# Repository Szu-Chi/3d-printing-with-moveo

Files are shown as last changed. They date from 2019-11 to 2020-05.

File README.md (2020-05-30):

# 3D printing with Moveo


### 將BCN3D-Moveo結合ROS、Marlin以及 Ultimaker Cura，產生新型態的3D列印機
我們變更3D列印切片軟體Cura的列印機模型與列印空間，並將Cura與ROS中的逆運動學求解器(IK-Slover)整合，把Cura生成的笛卡爾座標系轉換成更機械軸的轉動角度，最終透過Marlin控制BCN3D-Moveo移動噴嘴進行3D列印
### 系統架構 System Structure
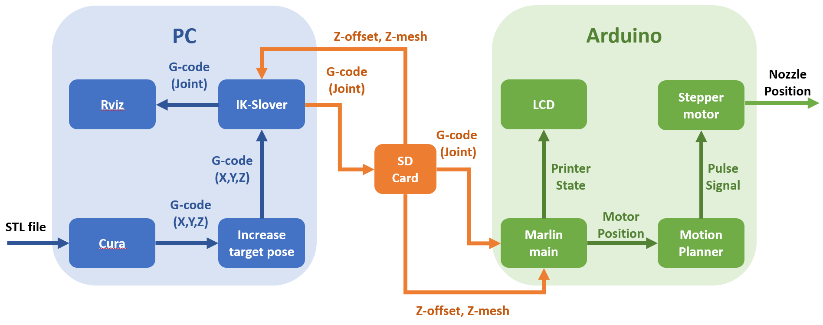
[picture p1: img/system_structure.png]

  
## Demonstration
### 1. 產生g-code與模擬
- 1. [使用Cura(SPIE Lab version)產生g-code](https://www.youtube.com/watch?v=-8nMFFa6ZWg)
- 2. [使用g-code模擬手臂列印](https://www.youtube.com/watch?v=KlCehcnmZSg)
- 3. [使用笛卡兒座標模擬手臂位置](https://www.youtube.com/watch?v=2ucYWZgq9BI)
- 4. [使用各軸轉動角度模擬手臂位置](https://www.youtube.com/watch?v=yYCW1fAp2H8)
### 2. 實際列印
| [寶箱](https://www.youtube.com/watch?v=BejQ-XHtku4) | [摩艾石像](https://www.youtube.com/watch?v=KtgakZhjTZc) | [20X20mm方框(厚度0.6mm)](https://www.youtube.com/watch?v=YZfbAIXzUUw) |
|:---:|:---:|:---:|
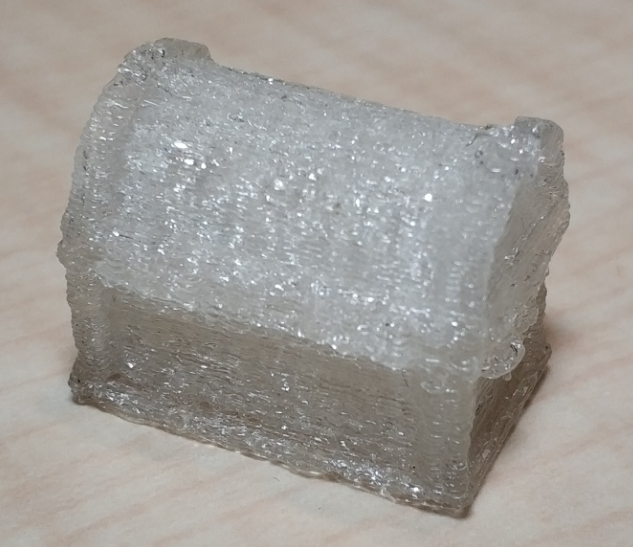
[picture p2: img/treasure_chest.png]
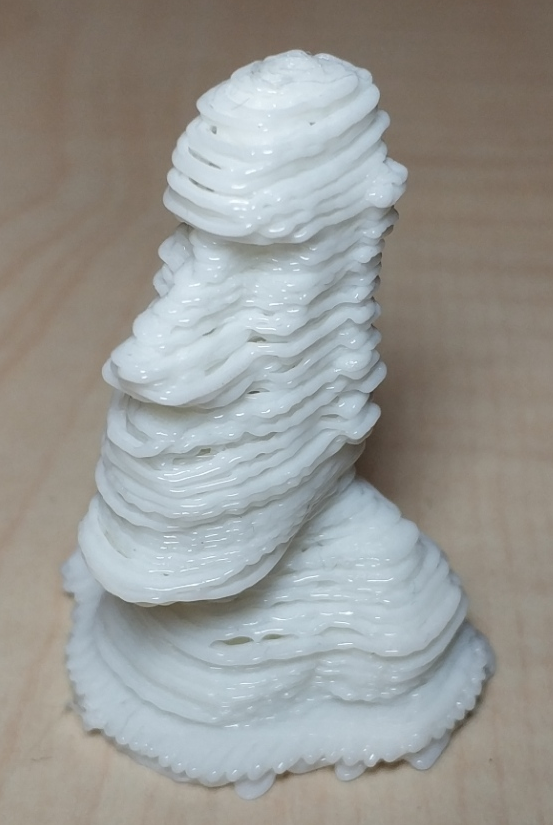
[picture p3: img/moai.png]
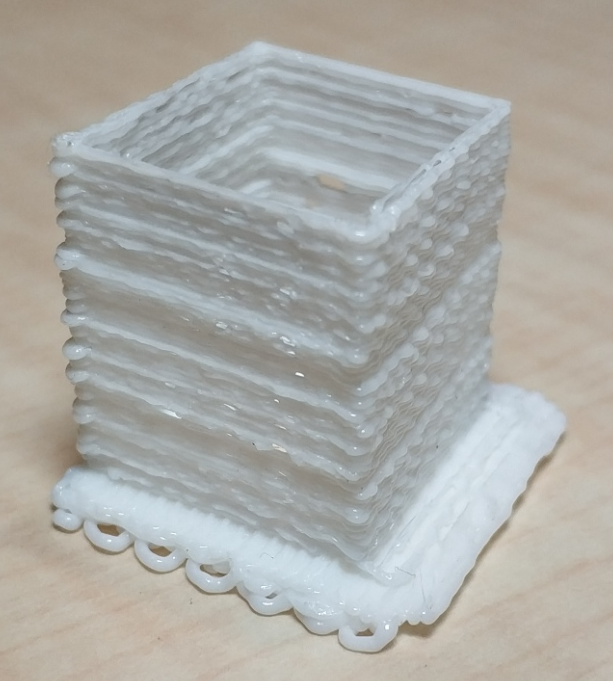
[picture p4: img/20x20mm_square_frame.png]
|  |  |  |
## How to Use
### 1. 環境準備
- 1. 安裝ROS、MoveIt和trac-ik
        1.  安裝ros-melodic-desktop-full\
            參考 [ROS-melodic](http://wiki.ros.org/melodic/Installation/Ubuntu)

        2.  使用原始碼安裝MoveIt\
            參考 [MoveIt](https://moveit.ros.org/install/source/)
        3.  安裝trac-ik
            ```
            sudo apt-get install ros-melodic-trac-ik
            ```
- 2. 建立工作區 moveo_ws
    ```
    cd ~
    mkdir moveo_ws 
    ``` 
- 3. 下載3d-printing-with-movoe資料
    ```
    cd ~/moveo_ws
    git clone https://github.com/Szu-Chi/3d-printing-with-moveo.git
    ``` 
- 4. 變更資料夾名稱為src
    ```
    mv ~/moveo_ws/3d-printing-with-moveo ~/moveo_ws/src
    ``` 
- 5. 建構原始碼build source code
    ```
    catkin_make
    source ~/moveo_ws/devel/setup.bash
    echo "source ~/moveo_ws/devel/setup.bash" >> ~/.bashrc
    ```

### 2. 安裝 Cura SPIE version
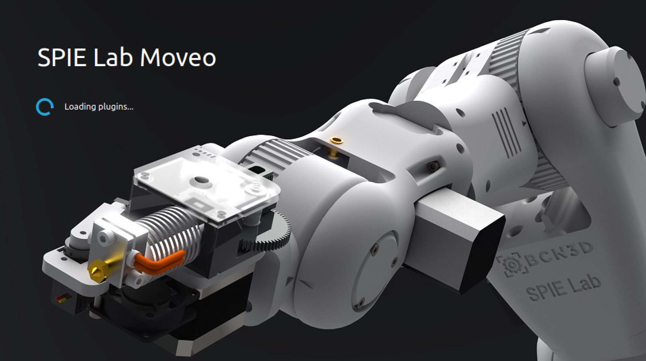
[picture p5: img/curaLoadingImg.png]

- 使用autoInstall.bash
    ```
    cd ~/moveo_ws/src/Cura
    bash autoInstall.bash
    source ~/.bashrc
    ```
or

- 參考 [Running-Cura-from-Source-on-Ubuntu](https://github.com/Ultimaker/Cura/wiki/Running-Cura-from-Source-on-Ubuntu) 手動安裝

### 3. 燒錄Marlin
- 1. 開啟Arduino ~/moveo_ws/src/Marlin/Marlin.ino
- 2. Tool->Board->Arduino Mega or Mega 2560
- 3. 按下上傳按鈕(Ctrl+U) 
### 4. 開始列印
- 1. 開啟Cura
    ```
    cura
    ```
- 2. 放入要列印的STL
- 3. 按下Slice開始切片
- 4. 存檔並等待G-code生成
- 5. 開啟3D列印機
- 6. Prepare->Auto home->Home ALL
- 7. Print from SD
- 8. 開始列印
## About Directories
### CAD
我們更改過後的Moveo，變更內容如下:
- 1. 加上Titan擠出軸以及噴頭組
- 2. 移除木板，新增旋轉台底座
- 3. 變更3M2和4M(加上齒輪組)
- 4. 增進4M1D與3M2之間的穩定度
- 5. 在機構內部新增走線空間

[BCN3D-Moveo 原始版本](https://github.com/BCN3D/BCN3D-Moveo)
### Cura
我們更改過後的Cura，變更內容如下:
- 1. 新增列印機型 SPIE Joint Lab Moveo
- 2. 在機型為Moveo時，改變空間界線判斷方式
- 3. 在機型為Moveo時，連接ROS轉換座標與機械軸位置

[Cura 原始版本](https://github.com/Ultimaker/Cura/wiki/Running-Cura-from-Source-on-Ubuntu) 
### Marlin
我們更改過後的Marlin，變更內容如下:
- 1. 變更Mother Board Arduino腳位
- 2. 馬達歸位方式
- 3. 平面測量方式
- 4. Motion Planner規劃方式

[Marlin 原始版本](https://github.com/MarlinFirmware/Marlin)
### circuit
- 1. Arduino 3D印表機擴充版電路圖及PCB layout\
     [RAMPSv1.6 原始版本](https://github.com/MarlinFirmware/Marlin)

- 2. 馬達閉迴路控制板電路圖及PCB layout\
     [uStepper 原始版本](https://github.com/uStepper/uStepper1)

### gcode_translation
將原始G-code的笛卡爾座標轉換成機械軸

### moveo_moveit_move_group
ROS中用來測試Moveo動作、列印範圍及IK解答效能

### moveo_moveit_config
使用MoveIt Setup Assistant設定Moveo的參數檔(如:各軸活動極限、虛擬機械軸、規劃運動群組...等)，此參數檔用於MoveIt
### moveo_urdf
由SolidWorks外掛模組SW2URDF所生成的Moveo的URDF(Unified Robot Description File)
### progressbar
在Cura切片時產生當前進度條
### simulation
讀取G-code中機械軸的位置，利用Rviz模擬Moveo列印情況
## Troubleshooting
-

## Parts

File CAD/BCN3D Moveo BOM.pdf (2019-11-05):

BCN3D Moveo BOM.xlsx

1

BOM ID | BOM | QUANTITY
1 | Stepper Motor SM42HT47-1684 1,8º step, 1,6 A, 3600 g·cm | 1
2 | ARDUINO MEGA 2560 | 1
3 | Stepper Driver tb6560 | 6
4 | Power Supply 24V 320W | 1
5 | RAMPS V1.4 | 1
6 | Power converter 24V a 12V | 1
7 | Servo Motor 180§ 55G TORQUE=13KG/CM | 1
8 | Gear Ratio 5:1 Planetary Gearbox Nema 17 Stepper 17HS19-1684S-PG5 ( step 0,35º , 2Nm, 1,68A) | 1
9 | Nema 23, 112mm, Ø8mm flat shaft SM57HT112-3004A, step 1,8º, 3A,28Kg·cm | 2
10 | Stepper Motor SM35HT36-1004A, 1,8º step, 1A, 1400g·cm | 1
11 | Stepper Motor nema 17 SM42HT33-1334, 1,8º step, 1,33A, 2200 g·cm | 1
12 | Chrome steel smooth bar-134mm | 1
13 | Chrome steel smooth bar-114mm | 1
14 | Chrome steel smooth bar-80mm | 1
15 | Ball Bearing 608ZZ 8mm x 22mm x 7mm | 10
16 | Ball Bearing 625ZZ 5mm x 16mm x 5mm | 8
17 | Ball Bearing 624ZZ 4mm x 13mm x 5mm | 9
18 | Ball Bearing 623ZZ 3mm x 10mm x 4mm | 3
19 | Brass insert M4 | 3
20 | Brass insert M3 | 20
21 | Pulley T5, Bore 8mm, 14 tooth, 17mm width | 3
22 | Pulley T5, Bore 5mm, 10 tooth, 17 mm width | 2
23 | ROD BAR M8 L 42mm | 1
24 | ZCOUPLING STEEL 5 TO 8 mm rigid | 1
25 | Axial Fan DC 24V 80x80mm | 1
26 | Axial Fan DC 24V 50x50mm | 1
27 | Powwer supply cable IEC 1,8m | 1
28 | Cable USB 2.0 AM/BM 1,8m | 1
29 | Cable Ties | 10
30 | Selfoil bearing 5mm x 8mm x 10mm | 8
31 | Selfoil bearing 8mm x 12mm x 20mm | 2
32 | Wood Base - 550mm x 550mm x 16mm | 1
33 | Breco belt T5, 16mm width, L 180cm | 1,8 m
101 | Dimension A: M-3 Dimension B: 10 mm | 30
102 | Dimension A: M-3 Dimension B: 12 mm | 6
103 | Dimension A: M-3 Dimension B: 16 mm | 13
104 | Dimension A: M-3 Dimension B: 20 mm | 4
105 | Dimension A: M-3 Dimension B: 25 mm | 5
106 | Dimension A: M-3 Dimension B: 30 mm | 2
107 | Dimension A: M-3 Dimension B: 40 mm | 7
108 | Dimension A: M-4 Dimension B: 12 mm | 2
109 | Dimension A: M-4 Dimension B: 10 mm | 2
110 | Dimension A: M-4 Dimension B: 16 mm | 8
111 | Dimension A: M-4 Dimension B: 40 mm | 4
112 | Dimension A: M-4 Dimension B: 45 mm | 6
113 | Dimension A: M-4 Dimension B: 60 mm | 4
114 | Dimension A: M-5 Dimension B: 14 mm | 120
115 | Dimension A: M-5 Dimension B: 20 mm | 8
116 | Dimension A: M-8 Dimension B: 65 mm | 1
117 | Dimension A: M-4 Dimension B: 25 mm | 4
118 | Dimension A: M-3 Nut | 30
119 | Dimension A: M-4 Nut | 4
120 | Dimension A: M-4 Locknut | 18
121 | Dimension A: M-5 Locknut | 16
122 | Dimension A: M-8 Locknut | 2

Components

Fasteners

BCN3D Moveo BOM.xlsx

2

123 | Dimension A: M-4 Dimension B: 20 mm | 3
124 | Dimension A: M-3 Dimension B: 8 mm | 4
125 | Dimension A: M-4 Dimension B: 30 mm | 8
126 | Dimension A: M-3 Dimension B: 35 mm | 4
127 | Washer M-3 | 10
| BOM ID | Parts | Name | Quantity
| 202 | Articulation 1 | 1M1 | 1
| 203 | | 1M2 | 1
| 204 | | 1M3 | 1
| 205 | Articulation 2 | 2M1 | 1
| 206 | | 2M2M | 1
| 207 | | 2M2H | 1
| 208 | | T2M1D | 1
| 209 | | T2M1I | 1
| 210 | Articulation 3 | 3M1 | 1
| 210A | | 3M2C | 1
| 211 | | 3M2 | 1
| 212 | | T3M1 | 1
| 213 | Articulation 4 | 4M1 | 1
| 214 | | 4M2 | 1
| 215 | | 4M2C | 1
| 216 | | T4M1 | 1
| 217 | Machine - tool | Top plate | 1
| 218 | | Bottom plate | 1
| 219 | | Cilinder | 2
| 220 | | Pivot arm | 1
| 221 | | Gripper left | 1
| 222 | | Gripper right | 1
| 223 | | Idol gear | 1
| 224 | | Servo gear | 1
| 225 | Box electronics | Box | 1
| 226 | | Fan module | 1
| 227 | | Suport Drivers | 1
| 228 | Base | Potes | 4
| 229 | Cover | Tapa 2M1 | 2
| 230 | | Tapa 3M1 | 2
| 231 | | Tapa 4M1 | 2
| 232 | | Tapa TBB | 1

Printed Parts

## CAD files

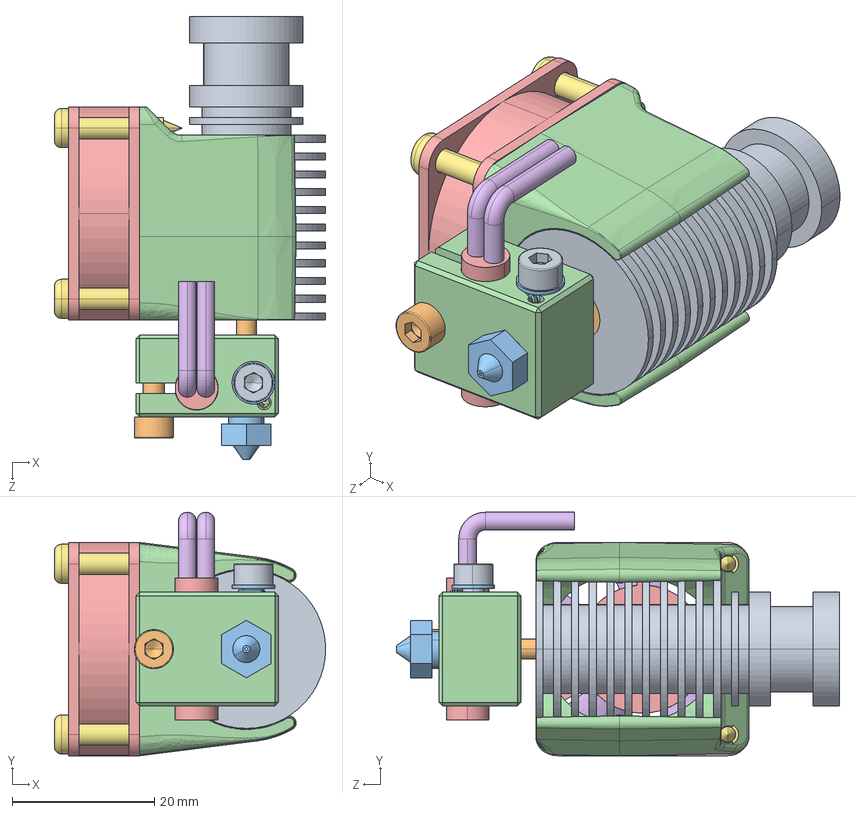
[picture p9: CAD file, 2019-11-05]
CAD/e3d-all-metal-hotend-v6-1.snapshot.2/E3D All Metal Hotend V6 assy.STEP
38.1 x 34.3 x 62.3 mm
E3D v6 HotEnd - Heatsink
E3D v6 HotEnd - Heatbreak
E3D v6 HotEnd - Nozzle
E3D v6 HotEnd - Heat Block
Ceramic Cartridge Heater
Thermistor
HEXAGON SOCKET HEAD CAP SCREWS_SCB3-4
HEXAGON SOCKET HEAD CAP SCREWS_SCB3-10
Flat Washers_PWF3
E3D-v6 Fan Duct
Fan-House-30x30x10-Promoco_Fan-House-KDE0503PFB3-Promoco
Fan-30x30x10-Promoco_Fan-KDE0503PFB3-Promoco
Self Tapping Screws - Pan Head_CSPTRSA-SUS-TP3-16 x 4

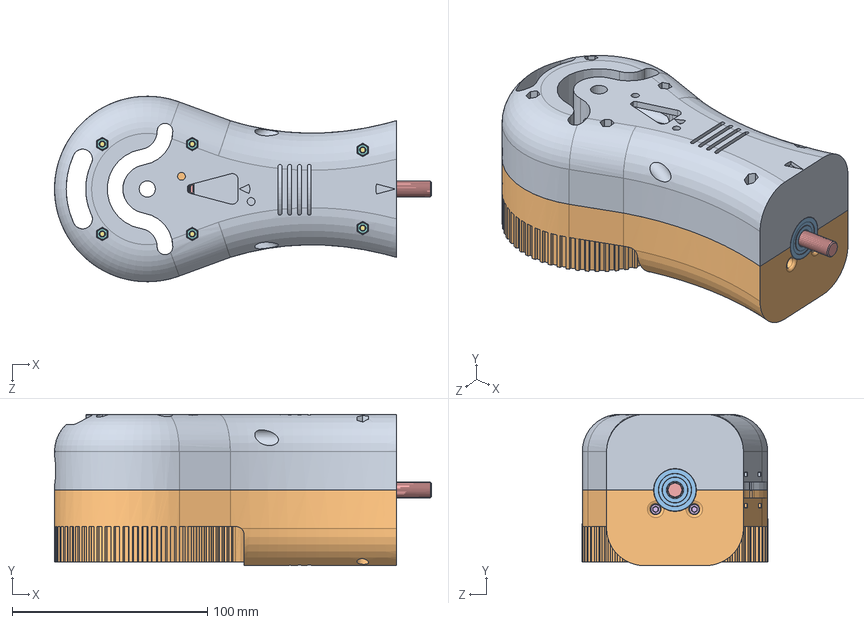
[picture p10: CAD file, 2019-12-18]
CAD/BCN3D-Moveo-master(1)/CAD files/3M2.SLDASM
193.0 x 77.5 x 95.0 mm
3M2C
3M2CC
8mm Bearing
Coupling 5 to 8 mm
Smooth bar 8mm x 50mm
M3x10 x 2
M3x40 x 6
M3 Nut x 6
35stepper with gearbox
limit button
Via Hole-Part-1 x 4
Pad U1-3(781.496mil,670.748mil) on Bottom Layer-Part-1
Track (945mil,777.5mil)(945mil,787.5mil) on Bottom Layer-Part-1
Track (932.5mil,765mil)(945mil,777.5mil) on Bottom Layer-Part-1
Track (922.5mil,765mil)(932.5mil,765mil) on Bottom Layer-Part-1
Track (878.248mil,720.748mil)(922.5mil,765mil) on Bottom Layer-Part-1
Track (781.496mil,720.748mil)(878.248mil,720.748mil) on Bottom Layer-Part-1
Pad U1-2(781.496mil,720.748mil) on Bottom Layer-Part-1
Pad C4-1(945mil,787.5mil) on Bottom Layer-Part-1
Track (470mil,610mil)(480.748mil,620.748mil) on Bottom Layer-Part-1
Track (480.748mil,620.748mil)(596.456mil,620.748mil) on Bottom Layer-Part-1
Pad U1-5(596.456mil,620.748mil) on Bottom Layer-Part-1
Pad R5-2(470mil,610mil) on Bottom Layer-Part-1
Track (910mil,955mil)(1010mil,955mil) on Bottom Layer-Part-1
Pad Hole-Part-1 x 36
Bottom Layer-Part-1 x 29
Top Layer-Part-1 x 29
Track (1010mil,260mil)(1010mil,455mil) on Bottom Layer-Part-1
Track (910mil,260mil)(910mil,455mil) on Bottom Layer-Part-1
Track (810mil,260mil)(810mil,455mil) on Bottom Layer-Part-1
Track (710mil,260mil)(710mil,455mil) on Bottom Layer-Part-1
Pad Copper-Part-1
Pad Copper-Part-1-1
Track (610mil,955mil)(652.5mil,912.5mil) on Bottom Layer-Part-1
Track (610mil,955mil)(610mil,1060mil) on Bottom Layer-Part-1
Track (652.5mil,912.5mil)(1057.5mil,912.5mil) on Bottom Layer-Part-1
Track (1057.5mil,912.5mil)(1079.472mil,890.528mil) on Bottom Layer-Part-1
Track (1118.158mil,606.842mil)(1118.158mil,649.528mil) on Bottom Layer-Part-1
Track (1079.472mil,688.213mil)(1118.158mil,649.528mil) on Bottom Layer-Part-1
Track (1079.472mil,688.213mil)(1079.472mil,890.528mil) on Bottom Layer-Part-1
Pad R2-1(610mil,1060mil) on Bottom Layer-Part-1
Track (1032.9mil,914.472mil)(1079.472mil,867.9mil) on Top Layer-Part-1
Track (710mil,955mil)(750.528mil,914.472mil) on Top Layer-Part-1
Track (750.528mil,914.472mil)(1032.9mil,914.472mil) on Top Layer-Part-1
Track (1079.472mil,745.528mil)(1120mil,705mil) on Top Layer-Part-1
Track (1079.472mil,745.528mil)(1079.472mil,867.9mil) on Top Layer-Part-1
Track (810mil,955mil)(854mil,999mil) on Top Layer-Part-1
Track (854mil,999mil)(1040mil,999mil) on Top Layer-Part-1
Track (1040mil,999mil)(1053.472mil,985.528mil) on Top Layer-Part-1
Track (1053.472mil,918.9mil)(1053.472mil,985.528mil) on Top Layer-Part-1
Track (1120mil,805mil)(1120mil,852.373mil) on Top Layer-Part-1
Track (1053.472mil,918.9mil)(1120mil,852.373mil) on Top Layer-Part-1
Track (510mil,955mil)(510mil,1055mil) on Bottom Layer-Part-1
Track (510mil,1055mil)(515mil,1060mil) on Bottom Layer-Part-1
Track (295mil,955mil)(510mil,955mil) on Bottom Layer-Part-1
Track (170mil,830mil)(295mil,955mil) on Bottom Layer-Part-1
Pad R1-1(515mil,1060mil) on Bottom Layer-Part-1
Pad Copper-Part-1-2
Pad Copper-Part-1-3
Track (572.905mil,872.725mil)(576.535mil,869.095mil) on Top Layer-Part-1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

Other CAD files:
CAD/BCN3D-Moveo-master(1)/CAD files/1M1A.SLDPRT
CAD/BCN3D-Moveo-master(1)/CAD files/1M1B.SLDPRT
CAD/BCN3D-Moveo-master(1)/CAD files/1M2A-1.SLDPRT
CAD/BCN3D-Moveo-master(1)/CAD files/1M2A-2.SLDPRT
CAD/BCN3D-Moveo-master(1)/CAD files/1M2A.SLDPRT
CAD/BCN3D-Moveo-master(1)/CAD files/1M3.SLDASM
CAD/BCN3D-Moveo-master(1)/CAD files/1M3A.SLDPRT
CAD/BCN3D-Moveo-master(1)/CAD files/2.SLDASM
CAD/BCN3D-Moveo-master(1)/CAD files/2M1D.SLDPRT
CAD/BCN3D-Moveo-master(1)/CAD files/2M2 assembly.SLDASM
CAD/BCN3D-Moveo-master(1)/CAD files/2M2HA.SLDPRT
CAD/BCN3D-Moveo-master(1)/CAD files/2M2M assembly.SLDASM
CAD/BCN3D-Moveo-master(1)/CAD files/2M2MA.SLDPRT
CAD/BCN3D-Moveo-master(1)/CAD files/2M_installHelper.SLDPRT
CAD/BCN3D-Moveo-master(1)/CAD files/35stepper with gearbox.SLDPRT
CAD/BCN3D-Moveo-master(1)/CAD files/3M1D.SLDPRT
CAD/BCN3D-Moveo-master(1)/CAD files/3M2C.SLDPRT
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

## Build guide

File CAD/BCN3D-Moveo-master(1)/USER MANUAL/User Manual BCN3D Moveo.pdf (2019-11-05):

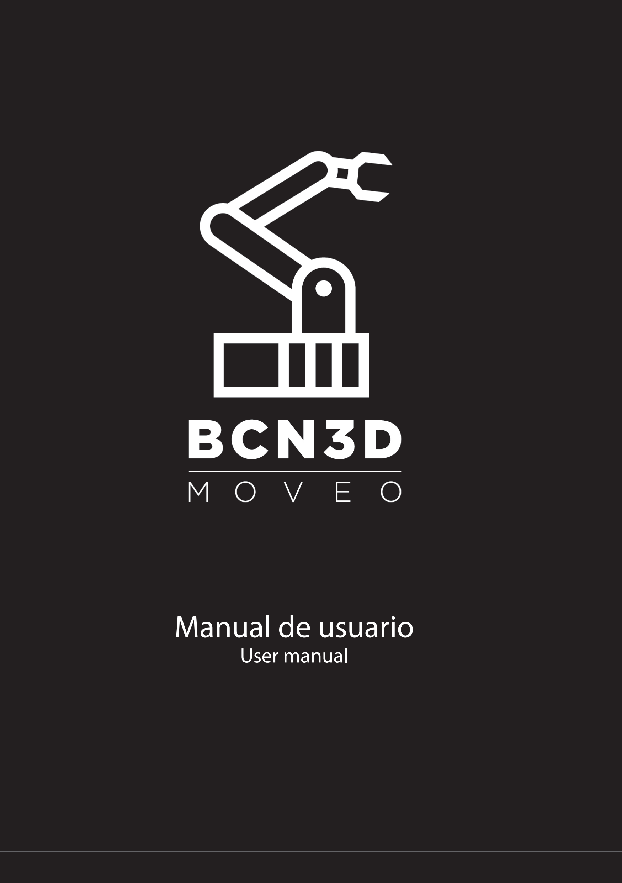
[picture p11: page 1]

# Manual de usuario

# User manual

2 - Manual de usuario User manual

Manual de montaje
Assembly manual

Manual de usuario User manual

¿Cómo usar el BCN3D Moveo? How to use the BCN3D Moveo?

Instalación del firmware
Firmware installation

Sobre el BCN3D Moveo
About de BCN3D Moveo

## ÍNDICE INDEX

3 - 4

6 - 39

40 - 42

43 - 45

Manual de usuario User manual - 3

## Sobre el BCN3D Moveo About the BCN3D Moveo

BCN3D Technologies sigue dando pasos importantes para cumplir con su objetivo de acercar las tecnologías de fabricación digital y aditiva al público general. En esta ocasión queremos presentar el BCN3D Moveo, un brazo robótico diseñado desde cero y desarrollado por nuestros ingenieros en colaboración con el Departament d’Ensenyament de la Generalitat de Catalunya, cuya estructura está impresa en 3D y su tecnología controlada por el software Arduino.
Moveo, totalmente funcional a día de hoy, ha nacido, como todos los demás productos salidos de BCN3D Technologies, con voluntad formativa y abierta.

EL PORQUÉ DE BCN 3D MOVEO

Una de las preocupaciones del Departament d’Ensenyament es el elevado coste de los materiales que deben usar los alumnos de formación de grado para realizar sus prácticas. En este sentido, un brazo robótico Open Source, modificable por los alumnos y reproducible a bajo coste podía copar varios de los itinerarios formativos existentes: Diseño mecánico, automatismos, programación industrial, etc.
Así pues, el BCN3D Moveo debería permitir a los institutos disfrutar de un equipamiento personalizable, modificable y de fácil acceso para el alumno a un precio lejos de los equipamientos industriales que normalmente habían tenido que adquirir, pero con unas prestaciones suficientes para los fines formativos.
Como área de la Fundació CIM, BCN3D Technologies comparte la vocación formativa de su alma máter. Es por dicho motivo que cuando el Departament d’Ensenyament se puso en contacto con nosotros para proponernos el proyecto un año atrás, no dudamos en aceptar la propuesta.
Una vez tuvimos el brazo diseñado y fabricado, se inició la última parte del proyecto que consistía en un workshop de montaje y puesta en marcha para 15 institutos de Cataluña, realizado en las instalaciones de BCN3D Technologies.
Estos institutos ya cuentan con el BCN3D Moveo en sus aulas y talleres, y deberán presentar prácticas que acrediten su conocimiento del equipo durante el mes de setiembre.

BCN3D Technologies keeps taking important steps in order to achieve his goal of bringing the digital manufacturing technology to everyone. In this occasion we are presenting the BCN3D Moveo, a robotic arm design from scratch and developed by our engineers in collaboration with the Departament d’Ensenyament from the Generalitat de Catalunya. Its structure is fully printed using additive manufacturing technologies and its electronics are controlled by the software Arduino.
Moveo, fully functional nowadays, has been born, as all the BCN3D Technologies products, with an open and educational wish.

WHY BCN 3D MOVEO

One of the Departament d’Ensenyament worries is the high price of the materials the grade students must use on their internships. Holding that in mind, an Open Source robotic arm, adaptable by the students and low cost reproducible could take several educational itineraries: mechanical design, automatism, industrial programing, etc.
Thus, the BCN3D Moveo should allow the educational centers to enjoy a modifiable and easily accessible for the students, at a price far lower than the usual industrial equipment they used to have to acquire, with enough output for training purposes. As a Fundació CIM area, BCN3D Technologies shares its educational vocation. That is the reason why when the Departament d’Ensenyament contacted us in order to suggest and offer this project a year ago we didn’t hesitate on taking that opportunity. Once we had the robotic arm designed and manufactured we started the last phase of the project, which consisted on an assembling and fine tuning workshop for 15 institutes around Catalonia, which took place in the BCN3D Technologies.
These institutes already have the BCN3D Moveo in their classrooms and workshops, and will have to present an internship program that proves their knowledge about the arm during September.

## Sobre el BCN3D Moveo About the BCN3D Moveo

TECNOLOGÍA OPEN SOURCE: LA PLATAFORMA
GITHUB

Como hiciéramos con todos nuestros productos, los archivos del BCN3D Moveo estarán a la disposición de todo aquel que quiera acceder a ellos. Gracias a la plataforma Github, un espacio en el que los usuarios comparten sus diseños de forma libre, cualquier persona podrá obtener toda la información necesaria para montarse su propio BCN3D Moveo en casa.
A diferencia de los otros productos de BCN3D Technologies, el BCN3D Moveo no será comercializado. El proyecto se ha realizado con el ánimo de dar una aportación más a la comunidad a partir de la idea del Departament d’Ensenyament.
BCN3D liberará el conocimiento del Moveo en sus repositorios en Github como se ha venido haciendo con los productos oficiales de BCN3D Techologies. De esta manera, se espera que la comunidad y los centros formativos que estén interesados puedan fabricar sus propios robots.
Así, entre los archivos que subiremos a dicha plataforma incluimos el “bill of materials” (BOM), en el que se detallan todos los componentes necesarios para montar el brazo, así como los diseños CAD, para que todo el mundo pueda modificar el diseño del BCN3D Moveo a su gusto. De la misma forma, los usuarios de Github podrán encontrar los archivos STL para la impresión de la estructura del brazo, y el manual de montaje del mismo que estará en español e inglés.
Gracias a este proyecto impulsado por el Departament d’Ensenyament y desarrollado por BCN3D Technologies, todo el mundo podrá fabricarse un brazo robótico en casa, sin necesidad de tener un amplio conocimiento técnico. Así, os animamos a todos a fabricaros el BCN3D Moveo y compartir los resultados en las redes con el hashtag #BCN3DMoveo.

OPEN SOURCE TECHNOLOGY: GITHUB

As we have done with all our developed pordutcs, the BCN3D Moveo files will be available for everyone. Thanks to the platform Github, a website where users around the world share their designs, anyone will be able to obtain all the necessary information in order to assemble his own BCN3D Moveo at home.
Unlike the other BCN3D products, the Moveo won’t be commercialized. The project has been born and developed in order to make a move for the community progress starting from the Departament d’Ensenyament idea.
Nevertheless, BCN3D will fee all the Moveo know how on our Github account, as we have been doing with all the BCN3D Technologies products. Thus, the users will be able to find the bill of material (BOM), where all the needed components for the assembling of the arm come detailed, as the CAD designs, so anyone will be able to modify the BCN3D Moveo design as they wish.
Furthermore, the Github users will find the STL files for the structure printing and the assembling, fine tuning and firmware upload manuals, which will be available both in English and Spanish.
Thanks to this project motivated by the Departament d’Ensenyament and developed by BCN3D Technologies everyone will be able to fabricate their own robotic arm at home, no highly technical knowledge needed. Therefore, we encourage you to fabricate the BCN3D Moveo and share the results on the social networks using the hashtag #BCN3DMoveo.

# Manual de montaje

# Assembly manual

## Montaje del módulo 1 Module 1

x8

BOM | Descripción Description | Cant Qty
115 | Tornillo M5 x 20mm Screw M5 x 20mm | 8
16 | Rodamiento 5mm x 16mm x 5mm Bearing 5mm x 16mm x 5mm | 8
30 | Espaciador 5mm x 10mm Spacer 5mm x 10mm | 8

121 | Tuerca autoblocante M5 M5 locknut | 8
15 | Rodamiento 8mm x 22mm x 7mm Bearing 8mm x 22mm x 7mm | 2
- | 1M2A Base rotatoria 1M2A Rotary plate | 1

## Montaje del módulo 1 Module 1 assembly

x1

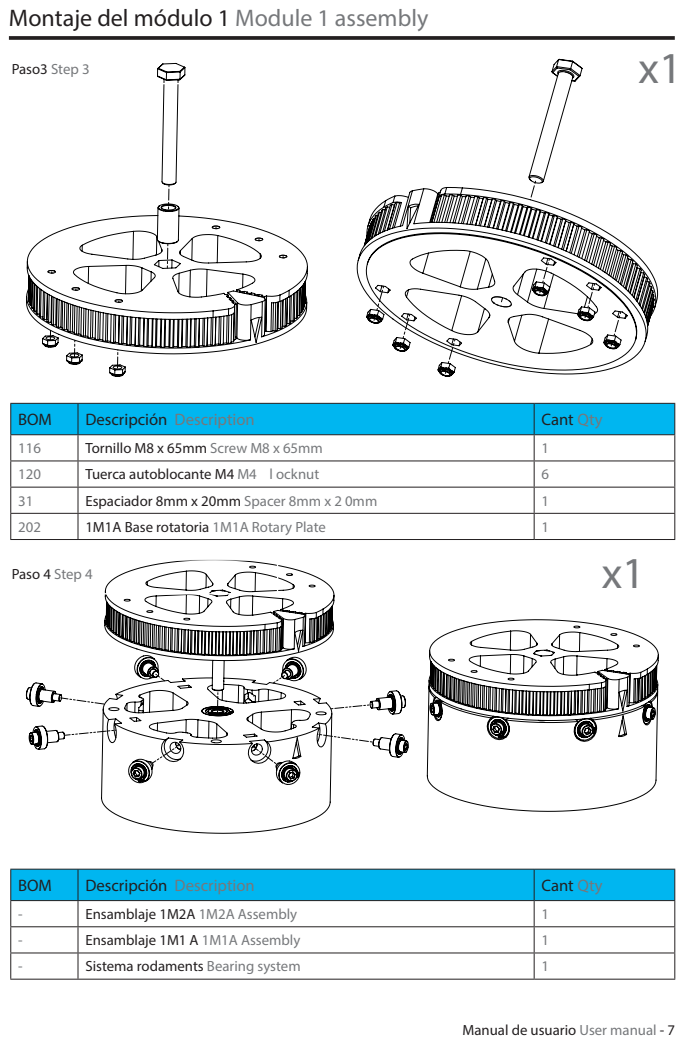
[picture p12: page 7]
Paso3 Step 3; Paso 4 Step 4

BOM | Descripción Description | Cant Qty
116 | Tornillo M8 x 65mm Screw M8 x 65mm | 1
120 | Tuerca autoblocante M4 M4 l ocknut | 6
31 | Espaciador 8mm x 20mm Spacer 8mm x 2 0mm | 1
202 | 1M1A Base rotatoria 1M1A Rotary Plate | 1

- | Ensamblaje 1M2A 1M2A Assembly | 1
- | Ensamblaje 1M1 A 1M1A Assembly | 1
- | Sistema rodaments Bearing system | 1

## Montaje del módulo 1 Module 1 assembly

BOM ID | Descripción Description | Cant Qty
204 | Pieza impresa 1M3 Printed part 1M3 | 1
1 | Motor nema 17 largo Large nema 17 motor | 1
101 | Tornillo M3 x 10mm M3 x 8mm screw | 4
22 | Polea 5mm 5mm pulley | 1

## Montaje del módulo 2 Module 2 assembly

x1

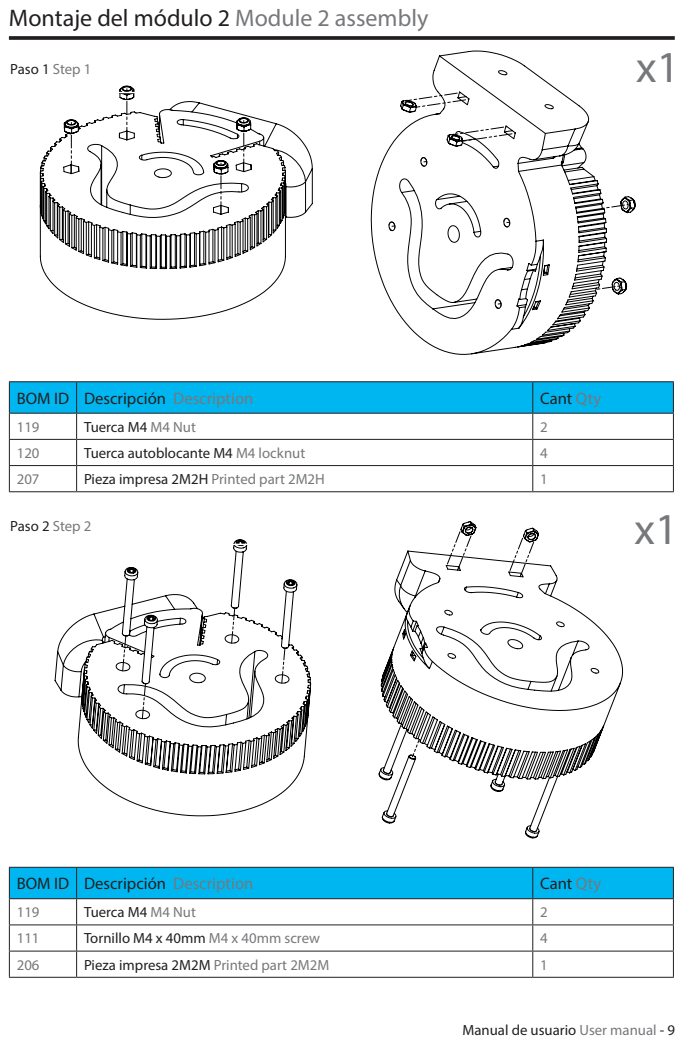
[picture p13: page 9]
Paso 1 Step 1; Paso 2 Step 2

BOM ID | Descripción Description | Cant Qty
119 | Tuerca M4 M4 Nut | 2
120 | Tuerca autoblocante M4 M4 locknut | 4
207 | Pieza impresa 2M2H Printed part 2M2H | 1

111 | Tornillo M4 x 40mm M4 x 40mm screw | 4
206 | Pieza impresa 2M2M Printed part 2M2M | 1

## Montaje del módulo 2 Module 2 assembly

BOM ID | Descripción Description | Cant Qty
- | Ensamblaje 2M2H 2M2H assembly | 2
- | Ensamblaje 2M2M 2M2M assembly | 2

## Montaje del módulo 2 Module 2 assembly

x1

BOM ID | Descripción Description | Cant Qty
208 | Pieza impresa T2M1D Printed part T2M1D | 1
117 | Tornillo M4 x 20mm M4 x 20mm screw | 1
119 | Tuerca M4 M4 nut | 1
118 | Tuerca M3 M3 nut | 1
17 | Rodamiento 4mm x 13mm x 5mm Bearing 4mm x 13mm x 5mm | 3

209 | Pieza impresa T2M1I Printed part T2M 1I | 1

## Montaje del módulo 2 Module 2 assembly

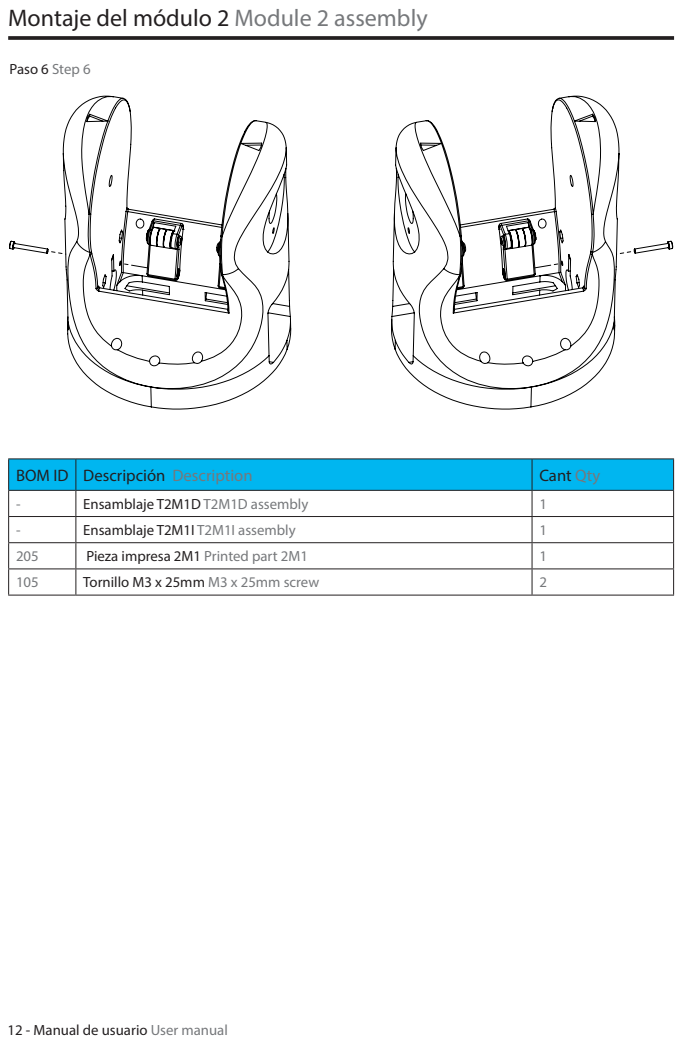
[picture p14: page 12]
Paso 6 Step 6

BOM ID | Descripción Description | Cant Qty
- | Ensamblaje T2M1D T2M1D assembly | 1
- | Ensamblaje T2M1I T2M1I assembly | 1
205 | Pieza impresa 2M1 Printed part 2M1 | 1
105 | Tornillo M3 x 25mm M3 x 25mm screw | 2

## Montaje del módulo 2 Module 2 assembly

BOM ID | Descripción Description | Cant Qty
9 | Motor Nema 23 Nema 23 motor | 2
114 | Tornillo M5 x 14mm M5 x 14mm screw | 8
121 | Tuerca autoblocante M5 M5 locknut | 8

## Montaje del módulo 2 Module 2 assembly

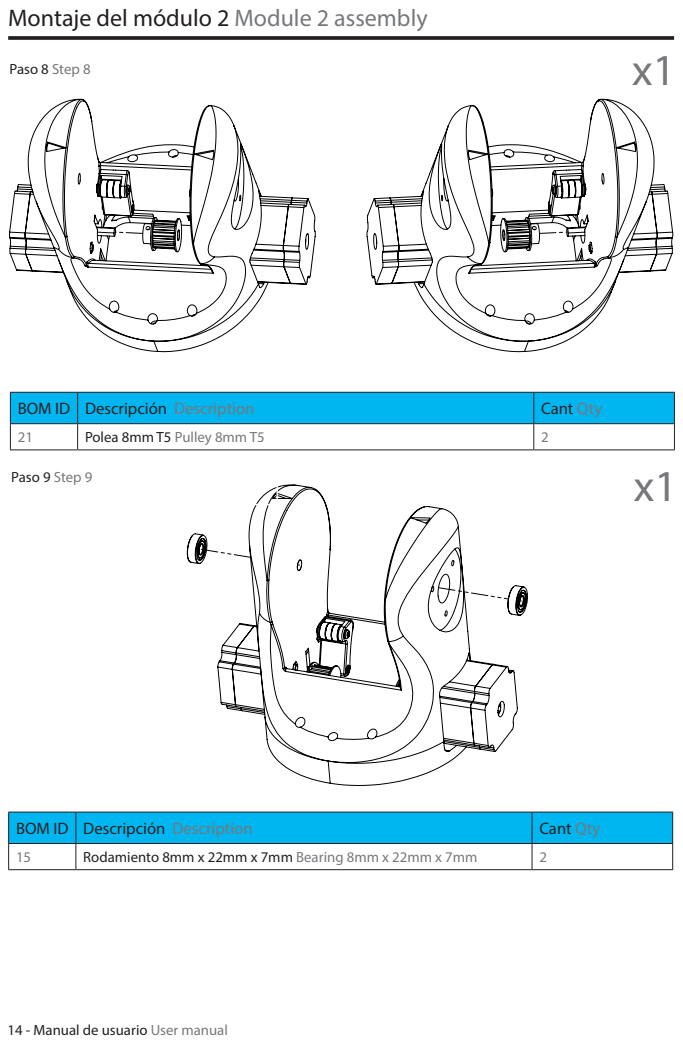
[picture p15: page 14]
Paso 8 Step 8; Paso 9 Step 9

BOM ID | Descripción Description | Cant Qty
21 | Polea 8mm T5 Pulley 8mm T5 | 2

15 | Rodamiento 8mm x 22mm x 7mm Bearing 8mm x 22mm x 7mm | 2

## Montaje del módulo 2 Module 2 assembly

BOM ID | Descripción Description | Cant Qty
- | Ensamblaje 2M2 2M2 assembly | 1

12 | Barra lisa 134mm Smooth bar 134mm | 1

## Montaje del módulo 2 Module 2 assembly

BOM ID | Descripción Description | Cant Qty
19 | Inserto M4 M4 insert | 2

20 | Inserto M3 M3 insert | 2
101 | Tornillo M3 x 10mm M3 x 10mm screw | 6
229 | Pieza impresa Tapa 2M1 Printed part Tapa 2M1 | 1

## Montaje de la herramienta Tool assembly

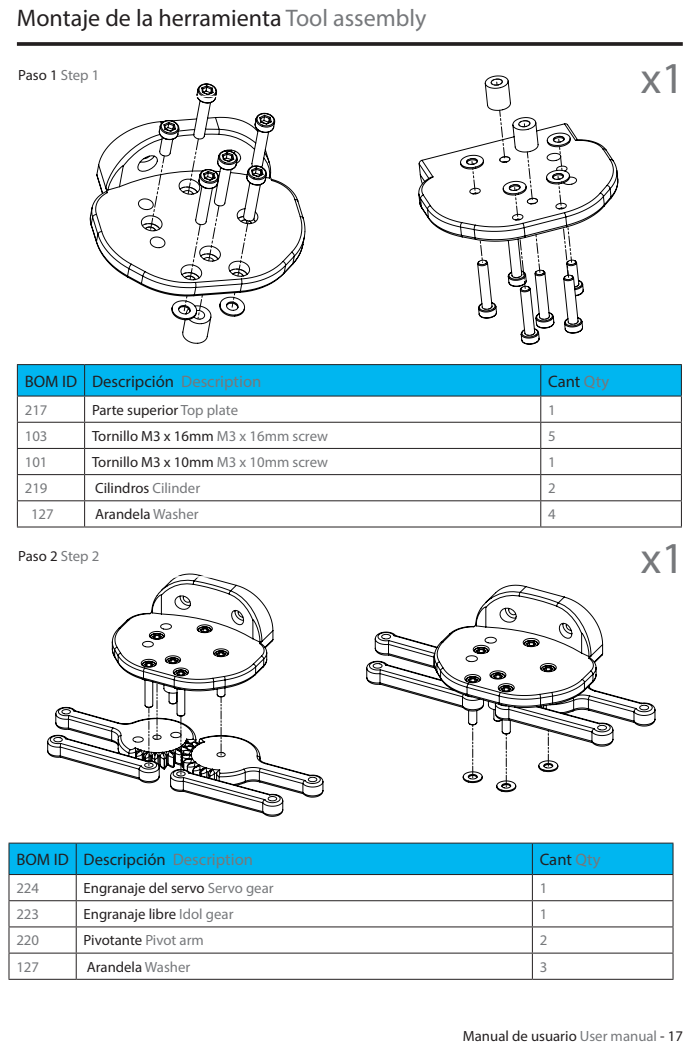
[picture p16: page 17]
Paso 1 Step 1; Paso 2 Step 2

BOM ID | Descripción Description | Cant Qty
217 | Parte superior Top plate | 1
103 | Tornillo M3 x 16mm M3 x 16mm screw | 5
101 | Tornillo M3 x 10mm M3 x 10mm screw | 1
219 | Cilindros Cilinder | 2
127 | Arandela Washer | 4

224 | Engranaje del servo Servo gear | 1
223 | Engranaje libre Idol gear | 1
220 | Pivotante Pivot arm | 2
127 | Arandela Washer | 3

## Montaje de la herramienta Tool assembly

BOM ID | Descripción Description | Cant Qty
218 | Parte inferior Bottom plate | 1
118 | Tuerca M3 M3 nut | 4

221 | Pinza izquiera Left gripper | 1
222 | Pinza derecha Right gripper | 1
103 | Tornillo M3 x 16mm M3 x 16mm screw | 8

## Montaje del módulo 3 Module 3 assembly

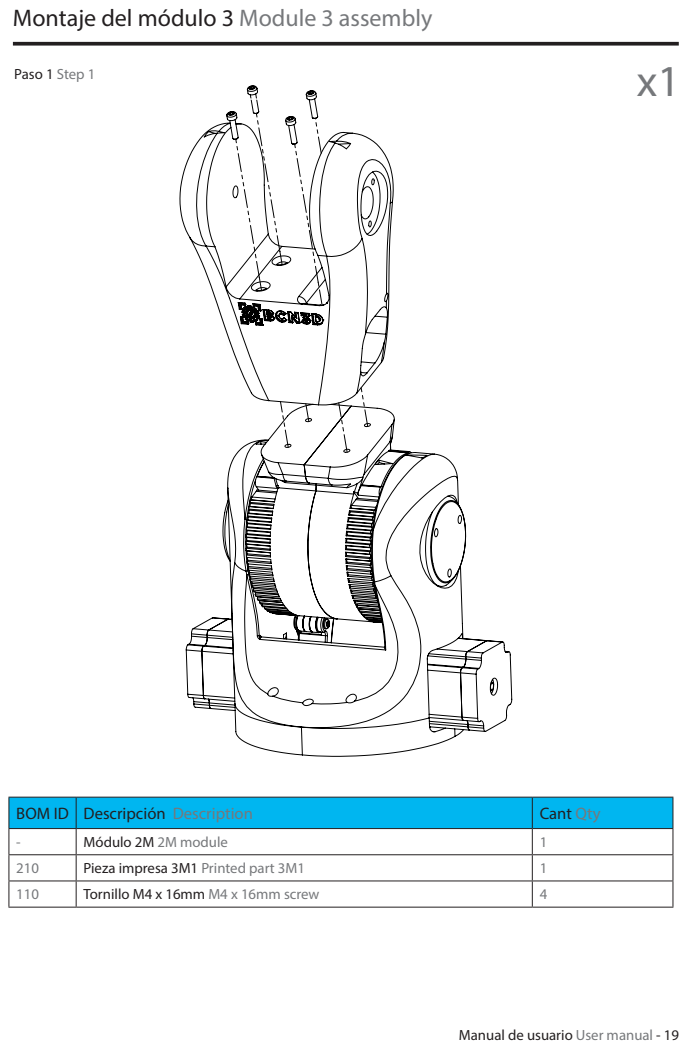
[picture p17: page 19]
Paso 1 Step 1

BOM ID | Descripción Description | Cant Qty
- | Módulo 2M 2M module | 1
210 | Pieza impresa 3M1 Printed part 3M1 | 1
110 | Tornillo M4 x 16mm M4 x 16mm screw | 4

## Montaje del módulo 3 Module 3 assembly

BOM ID | Descripción Description | Cant Qty
212 | Pieza impresa T3M1 Printed part T3M1 | 1
17 | Rodamiento 4mm x 13mm x 5mm Bearing 4mm x 13mm x 5mm | 3
123 | Tornillo M4 x 20mm M4 x 20mm screw | 1
119 | Tuerca M4 M4 nut | 1

- | Módulo T3M1 T3M1 module | 1
107 | Tornillo M3 x 40mm M3 x 40mm screw | 1
118 | Tuerca M3 M3 nut | 1

## Montaje del módulo 3 Module 3 assembly

BOM ID | Descripción Description | Cant Qty
210A | Pieza impresa 3M2C Printed part 3M2C | 1
11 | Motor Nema-17 34mm Nema-17 motor 34mm | 1
101 | Tornillo M3 x 10mm M3 x 10mm screw | 2

24 | Acoplador 8mm - 5mm Coupling 8mm- 5mm | 1
23 | Barra roscada 42mm Rod bar 42mm | 1
15 | Rodamiento 8mm x 22mm x 7mm Bearing 8mm x 22mm x 7mm | 1

## Montaje del módulo 4 Module 4 assembly

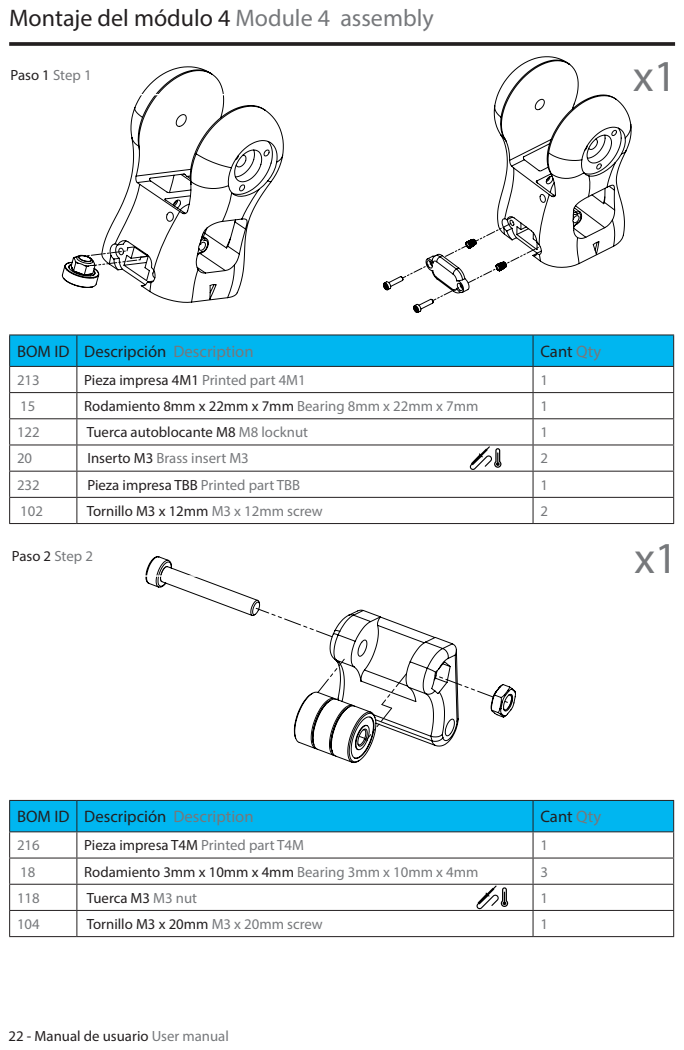
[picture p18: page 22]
Paso 1 Step 1; Paso 2 Step 2

BOM ID | Descripción Description | Cant Qty
213 | Pieza impresa 4M1 Printed part 4M1 | 1
15 | Rodamiento 8mm x 22mm x 7mm Bearing 8mm x 22mm x 7mm | 1
122 | Tuerca autoblocante M8 M8 locknut | 1
20 | Inserto M3 Brass insert M3 | 2
232 | Pieza impresa TBB Printed part TBB | 1
102 | Tornillo M3 x 12mm M3 x 12mm screw | 2

216 | Pieza impresa T4M Printed part T4M | 1
18 | Rodamiento 3mm x 10mm x 4mm Bearing 3mm x 10mm x 4mm | 3
118 | Tuerca M3 M3 nut | 1
104 | Tornillo M3 x 20mm M3 x 20mm screw | 1

## Montaje del módulo 4 Module 4 assembly

BOM ID | Descripción Description | Cant Qty
214 | Pieza impresa 4M2 Printed part 4M2 | 1
215 | Pieza impresa 4M2C Printed part 4M2C | 1
118 | Tuerca M3 M3 nut | 3
117 | Tornillo M4 x 25mm M4 x 25mm screw | 2
120 | Tuerca autoblocante M4 M4 Locknut | 4

## Montaje del módulo 4 Module 4 assembly

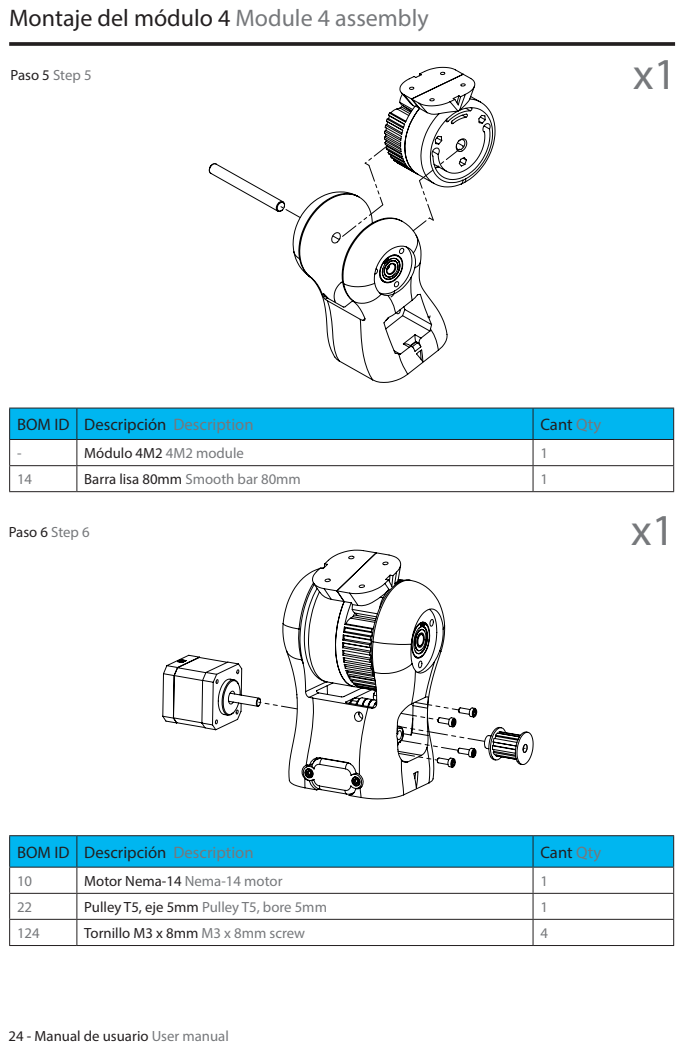
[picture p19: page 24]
Paso 5 Step 5; Paso 6 Step 6

BOM ID | Descripción Description | Cant Qty
- | Módulo 4M2 4M2 module | 1
14 | Barra lisa 80mm Smooth bar 80mm | 1

10 | Motor Nema-14 Nema-14 motor | 1
22 | Pulley T5, eje 5mm Pulley T5, bore 5mm | 1
124 | Tornillo M3 x 8mm M3 x 8mm screw | 4

## Montaje del módulo 4 Module 4 assembly

BOM ID | Descripción Description | Cant Qty
20 | Inserto M3 M3 insert | 6
231 | Pieza impresa Tapa 4M1 Printed part tapa 4M1 | 6
102 | Tornillo M3 x 12mm M3 x 12mm screw | 2

- | Módulo herramienta Tool module | 1
103 | Tornillo M3 x 16mm M3 x 16mm screw | 4

## Montaje del módulo 4 Module 4 assembly

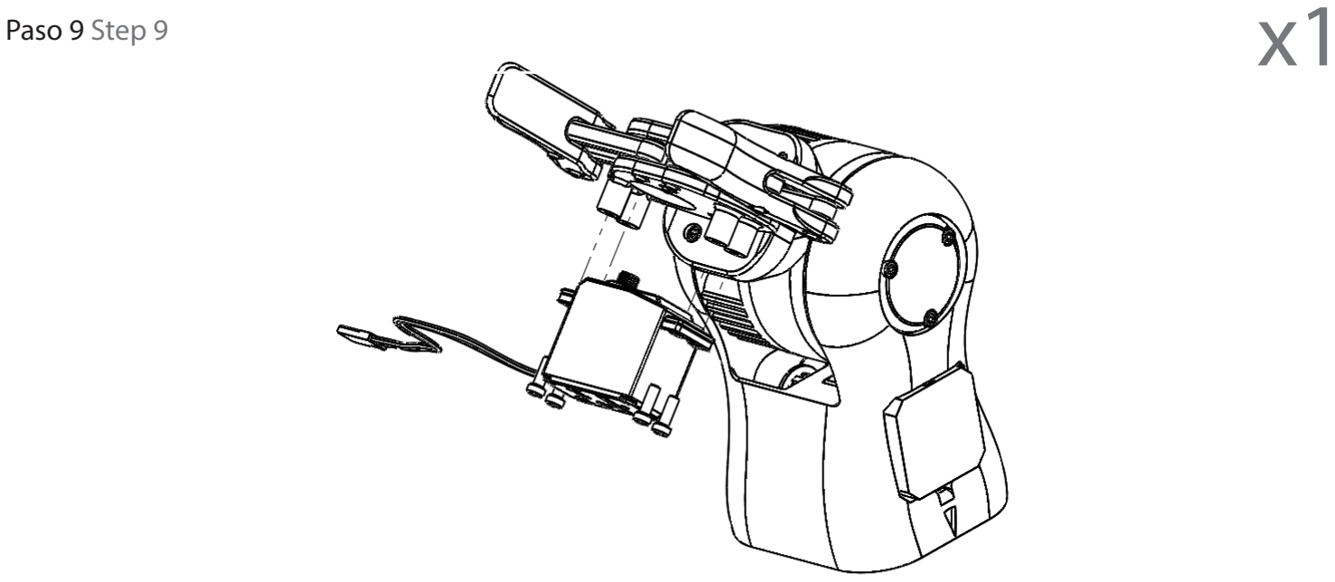
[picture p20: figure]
Paso 9 Step 9

BOM ID | Descripción Description | Cant Qty
7 | Servo motor Servo motor | 1
101 | Tornillo M3 x 10mm M3 x 10mm screw | 4

## Montaje del módulo 3 Module 3 assembly

BOM ID | Descripción Description | Cant Qty
- | Ensamblaje módulo 4 Tool module | 1
103 | Tornillo M3 x 16mm M3 x 16mm screw | 4

## Montaje del módulo 3 Module 3 assembly

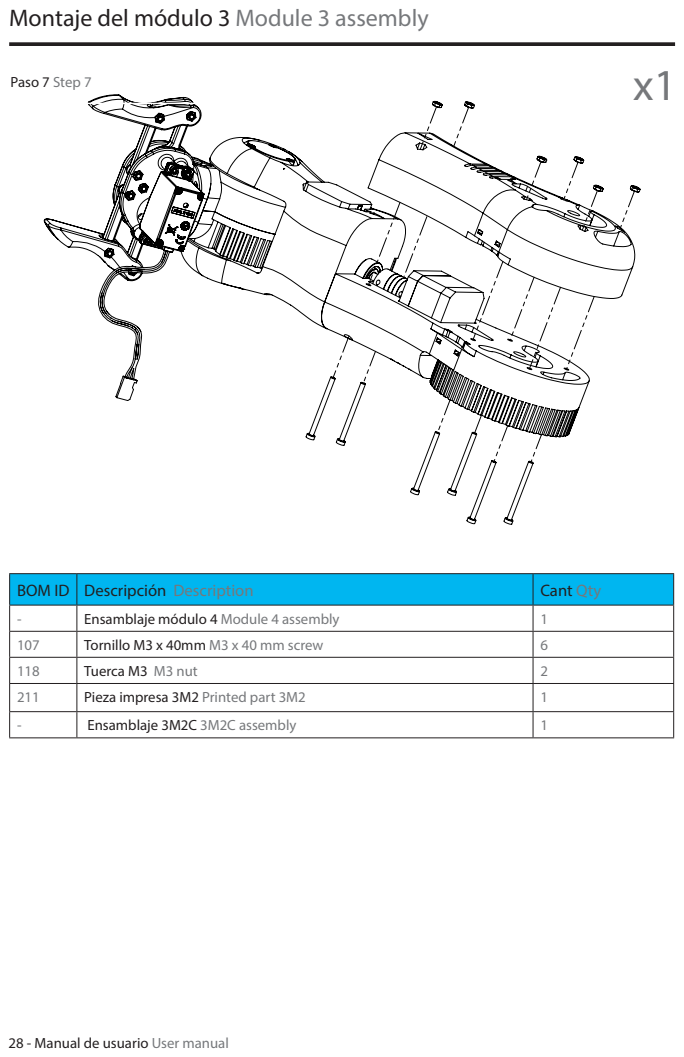
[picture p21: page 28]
Paso 7 Step 7

BOM ID | Descripción Description | Cant Qty
- | Ensamblaje módulo 4 Module 4 assembly | 1
107 | Tornillo M3 x 40mm M3 x 40 mm screw | 6
118 | Tuerca M3 M3 nut | 2
211 | Pieza impresa 3M2 Printed part 3M2 | 1
- | Ensamblaje 3M2C 3M2C assembly | 1

## Montaje del módulo 3 Module 3 assembly

BOM ID | Descripción Description | Cant Qty
15 | Rodamiento 8mm x 22mm x 7mm Bearing 8mm x 22mm x 7mm | 2

## Montaje del módulo 3 Module 3 assembly

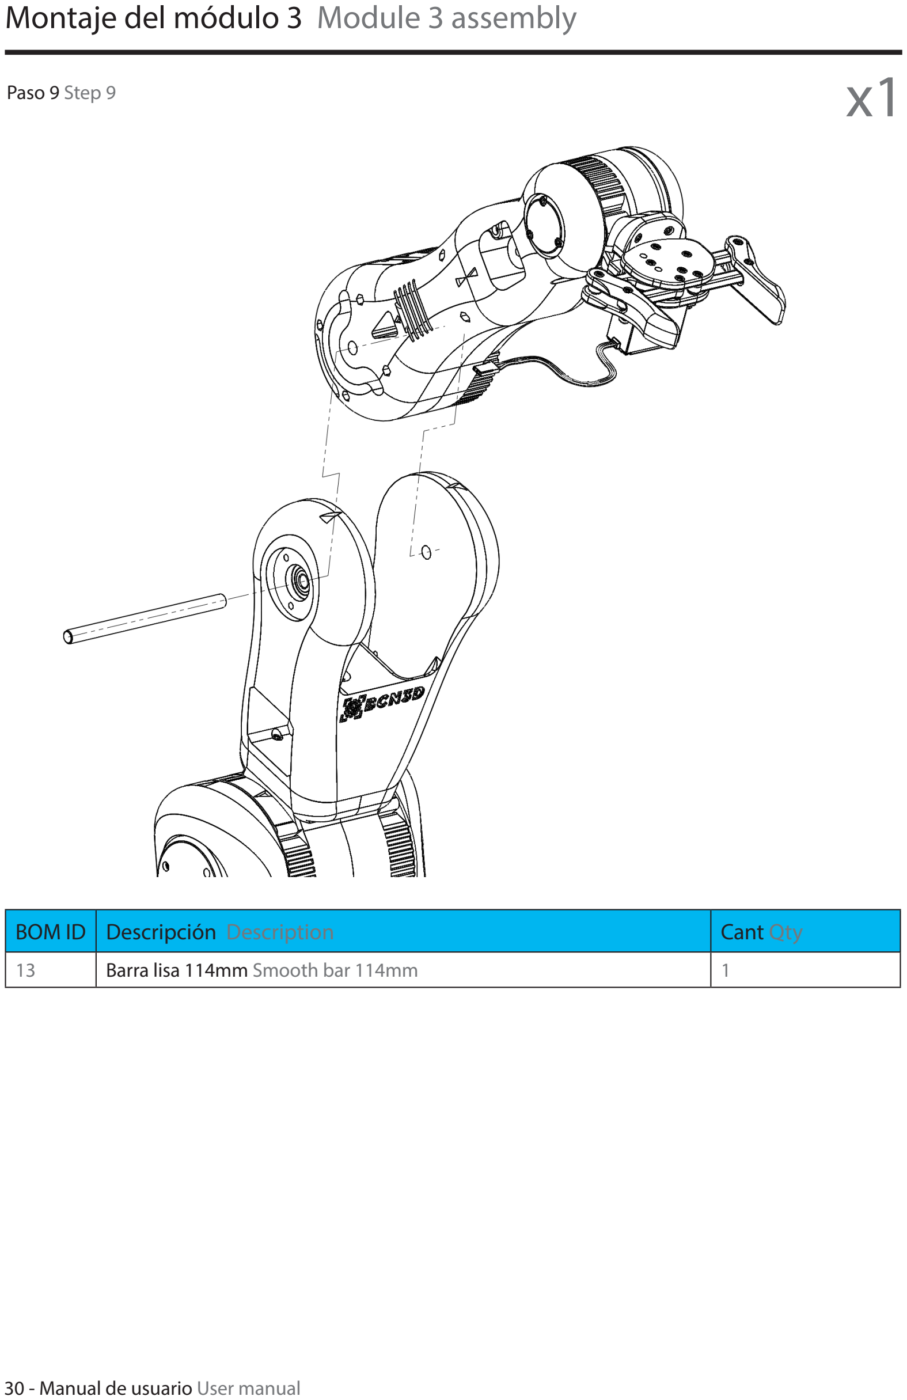
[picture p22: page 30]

BOM ID | Descripción Description | Cant Qty
13 | Barra lisa 114mm Smooth bar 114mm | 1
Paso 9 Step 9 | x1

## Montaje del módulo 3 Module 3 assembly

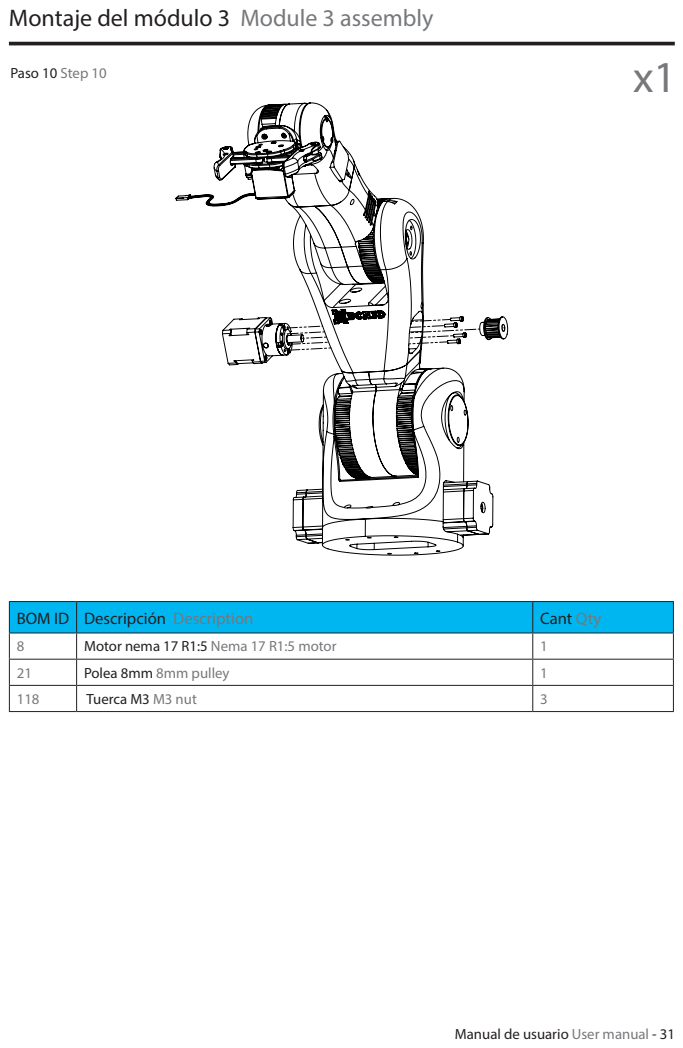
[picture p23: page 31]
Paso 10 Step 10

BOM ID | Descripción Description | Cant Qty
8 | Motor nema 17 R1:5 Nema 17 R1:5 motor | 1
21 | Polea 8mm 8mm pulley | 1
118 | Tuerca M3 M3 nut | 3

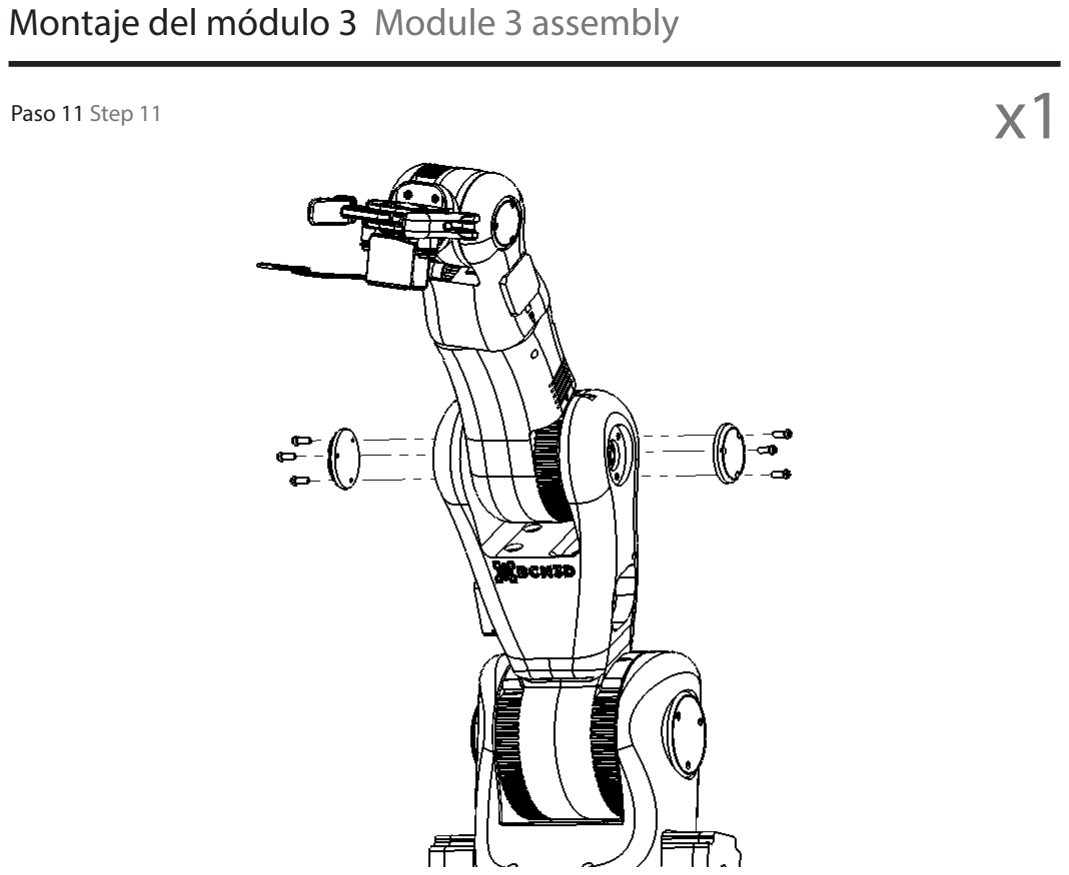
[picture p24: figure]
Montaje del módulo 3 Module 3 assembly; Paso 11 Step 11

BOM ID | Descripción Description | Cant Qty
230 | Pieza impresa tapa 3M1 Printed part tapa 3M1 | 2
101 | Tronillo M3 x 10mm M3 x 10mm srew | 1

## Montaje de la base Base assembly

BOM ID | Descripción Description | Cant Qty
- | Módulo 1M2 1M2 module | 1
32 | Base 550mm x 550mm 550mm x 550mm base | 1
111 | Tornillo M4 x 40mm M4 x 40mm screw | 4
120 | Tuerca autoblocante M4 M4 locknut | 2

## Montaje de la base Base assembly

BOM ID | Descripción Description | Cant Qty
- | Módulo 1M1 1M1 module | 1
112 | Tronillo M4 x 45mm M4 x 45mm srew | 6

## Montaje de la base Base assembly

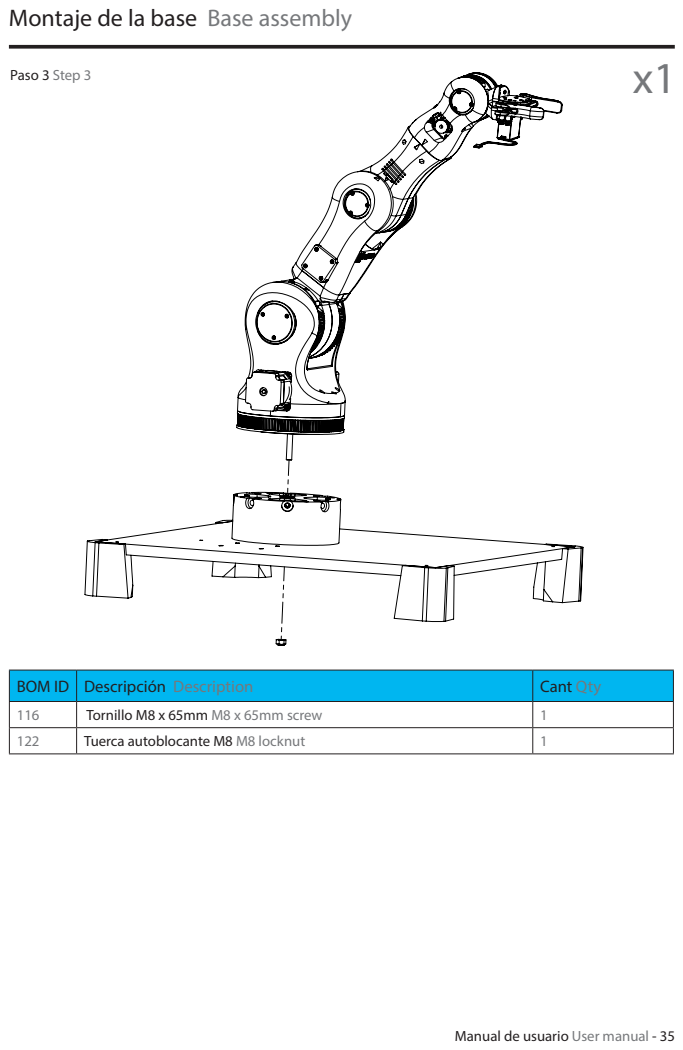
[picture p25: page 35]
Paso 3 Step 3

BOM ID | Descripción Description | Cant Qty
116 | Tornillo M8 x 65mm M8 x 65mm screw | 1
122 | Tuerca autoblocante M8 M8 locknut | 1

## Montaje de la base Base assembly

BOM ID | Descripción Description | Cant Qty
- | Módulo 1M3 1M3 module | 1
120 | Tuerca autoblocante M4 M4 locknut | 4
125 | Tornillo M4 x 30mm M4 x 30mm screw | 4

## Conexionado Connections

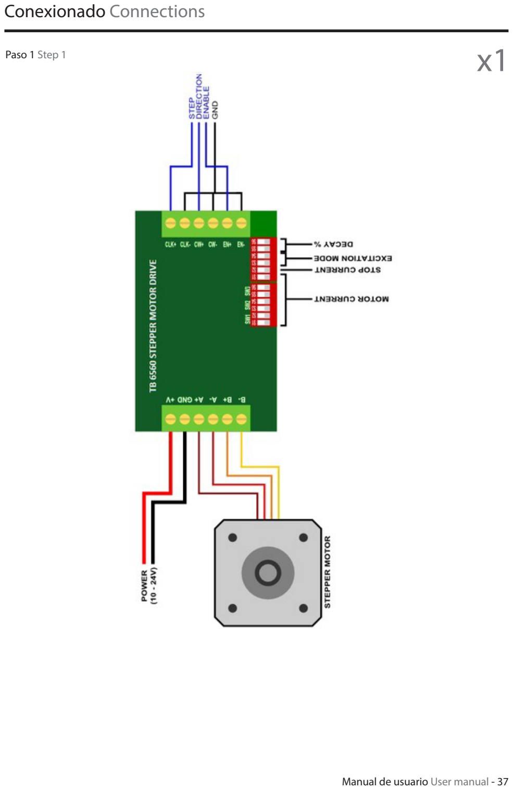
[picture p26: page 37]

Paso 1 Step 1 | x1

## Montaje de la base Base assembly

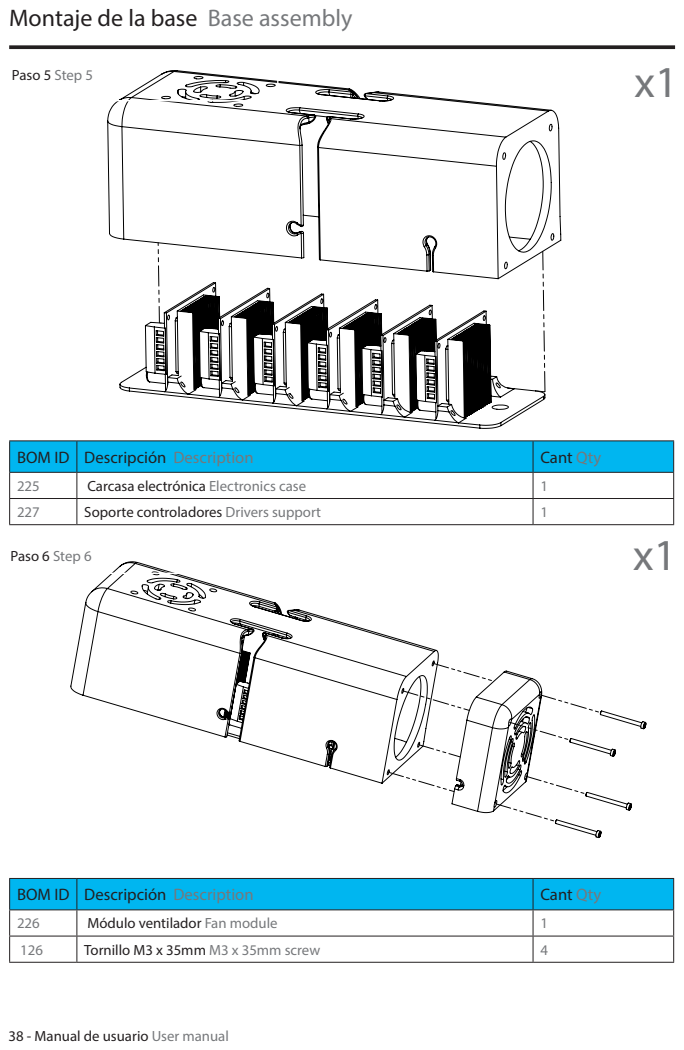
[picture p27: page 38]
Paso 5 Step 5; Paso 6 Step 6

BOM ID | Descripción Description | Cant Qty
225 | Carcasa electrónica Electronics case | 1
227 | Soporte controladores Drivers support | 1

226 | Módulo ventilador Fan module | 1
126 | Tornillo M3 x 35mm M3 x 35mm screw | 4

## Montaje de la base Base assembly

BOM ID | Descripción Description | Cant Qty
- | Módulo caja electrónica Electronics case module | 1
125 | Tornillo M4 x 30mm M4 x 30mm screw | 2

## Instalación del firmware Firmware installation

Arduino IDE

Arduino IDE es una plataforma que permite escribir código en un entorno limpio y ordenado. Una vez terminado podemos cargarlo en el arduino con solo pulsar un botón.
Estos són los passos a seguir para cargar el firmware. En nuestro caso, el firmware se llama “Marlin_BCN3D_Moveo” y está en una carpeta llamada Firmware.

Arduino IDE

Arduino IDE is a platform that allows you to write code in a clean and tidy environment. Once the code is written it, we can upload it to the arduino with just touching a button.
These are the steps to load the firmware. In our case, the firmware is called “Marlin_BCN3D_Moveo” and is located in a folder called Firmware.

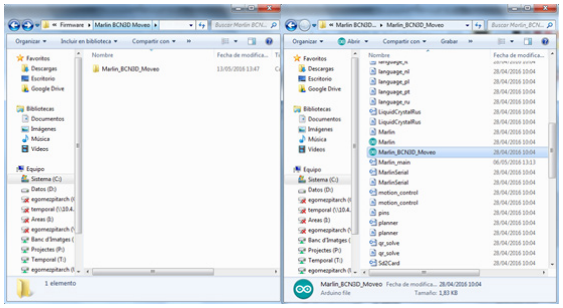
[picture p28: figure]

Una vez localizado el archivo “Marlin_BCN3D_Moveo.ino” hacer doble click en él para abrirlo. Cuando se haya cargado hacer click en herramientas y dirigirse a los apartados de “Placa”, “Procesador” y “Puerto”. Conectamos el Arduino en el PC. Abrimos el apartado de placa y seleccionamos nuestro modelo, Arduino Mega 2560.

Once you have located “Marlin_BCN3D_Moveo. ino” file, double-click on it to open it.
Click “Tools”, go to “Board”, and select Arduino Mega 2560.

## Instalación del firmware Firmware installation

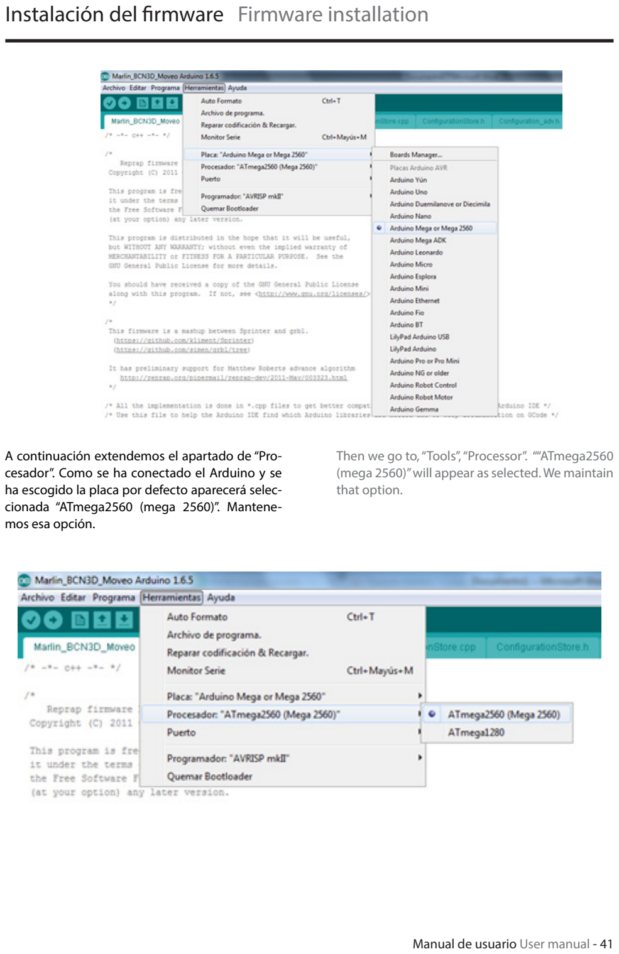
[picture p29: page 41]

A continuación extendemos el apartado de “Procesador”. Como se ha conectado el Arduino y se ha escogido la placa por defecto aparecerá seleccionada “ATmega2560 (mega 2560)”. Mantenemos esa opción.

Then we go to, “Tools”, “Processor”. ““ATmega2560 (mega 2560)” will appear as selected. We maintain that option.

## Instalación del firmware Firmware installation

El último parámetro es el del puerto. Hay que seleccionar el puerto que contenga el modelo de nuestra placa en el nombre, por ejemplo COM16 “Arduino Mega or Mega 2560”.

The last parameter is the “Tools”, “port”. You have to select the port that contains the model of your plaque in the name, eg COM16 “Arduino Mega or Mega 2560”.

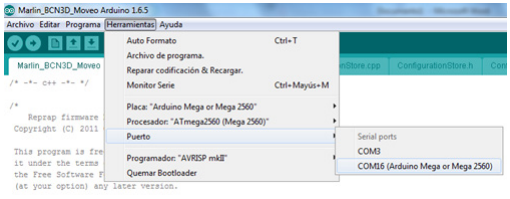
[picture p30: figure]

Para acabar hay que hacer click en botón de subir. Después de aproximadamente 1 minuto el firmware se habrá subido correctamente. Si hay problemas en la compilación descargar los drivers más actualizados desde la web de Arduino.

Finally, you must click the button “upload”. After about 1 minute firmware will be uploaded. If there are problems in the compilation, download the most current drivers from the website of Arduino.

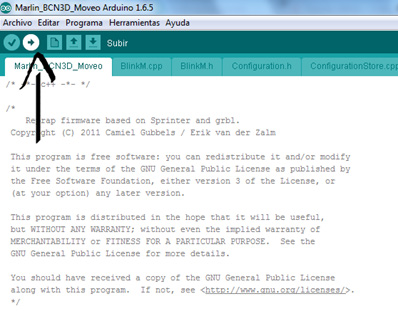
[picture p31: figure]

## ¿Cómo usar el BCN3D Moveo? How to use the BCN3D Moveo?

Pronterface

Pronterface es un programa destinado al testeo de impresoras 3D. Con él se pueden mover todos los ejes individualmente hacia todas las direcciones y también los extrusores. En la parte derecha hay un terminal de comandos con el que se pueden enviar líneas de gcode para mover los motores, leer las posiciones de cada motor y mover servo motores.
En nuestro caso, haremos uso del software Pronterface con el objetivo de mover el BCN3D Moveo. Para poder actuar sobre el BCN3D Moveo hay que establecer una comunicación entre Pronterface y el Arduino. Esto se consigue realizando los siguientes pasos. Primero se tiene que escoger el puerto COM en el que esté conectado el arduino.

Pronterface

Pronterface is a program for the testing of 3D printers. With it you can move all axes individually in all directions and also the extruders of your printer. On the right side of the program, there is a terminal command with which you can send gcode lines to move steppers, read the positions of each stepper and also move servo motors.
In our case, we will use the software Pronterface in order to move the BCN3D Moveo. To act on the BCN3D Moveo we must establish communication between Pronterface and Arduino. This is accomplished by performing the following steps.

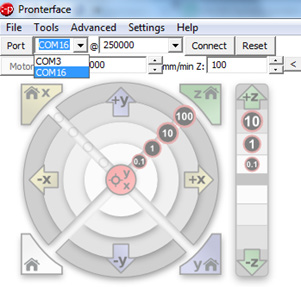
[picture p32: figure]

Atención: No se deben tener abiertos los dos programas (Pronterface y Arduino IDE) a la vez.

Please note that should not be open both programs (Pronterface and Arduino IDE) simultaneously.

## ¿Cómo usar el BCN3D Moveo? How to use the BCN3D Moveo?

El siguiente paso es escoger una velocidad de
250.000 baudios.

The next step is to choose a speed of 250,000 baud.

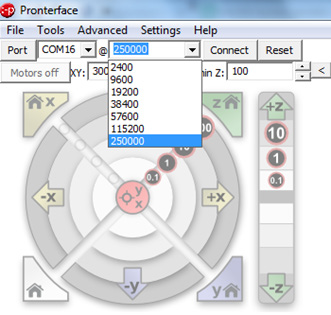
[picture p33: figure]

Finalmente para acabar de realizar la conexión hacer click en el botón “Connect”. Entre otras cosas aparecerá un texto notificando que nuestra impresora ya está online “Printer is now online”. A partir de ese momento se activará la función del terminal (situada en la parte inferior derecha) y la de mover los motores.
El círculo superior izquierdo nos muestra 3 de los 5 ejes (los principales). Con el movimiento de esos 3 ejes se pueden realizar aproximaciones y tests para encontrar las posiciones que más se adecúen a la secuencia de trabajo que se requiera. Una vez se hayan encontrado las posiciones el procedimiento es el de escribir un Gcode que contenga toda esa información.

Finally, to finish the connection, click the “Connect” button. Among other things, a text will appear notifying you that your printer is online “Printer is now online.”
From that moment, the function of the terminal (located on the bottom right) and the function of moving the motors will be activated.
The upper left circle shows 3 of the 5 axis (the main axis). With the movement of those 3 axes you can perform tests to find approaches and positions that are most suited to the sequence of work required. Once the positions have been found, the procedure is to write a .Gcode containing all this information.

## ¿Cómo usar el BCN3D Moveo? How to use the BCN3D Moveo?

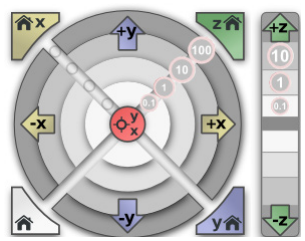
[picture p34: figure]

En éste círculo también se aprecian distintos valores, del 0.1 al 100. La unidad usada en los valores se refiere a un paso de los motores. Por norma general, cuando estamos testeando no se recomienda usar las opciones de 100 pasos.

In this circle also they appreciate different values, from 0.1 to 100. The unit used in the securities refers to a step of the engines. Generally, when we are testing, it is not recommended to use options 100 steps.

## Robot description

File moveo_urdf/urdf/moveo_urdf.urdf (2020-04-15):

<?xml version="1.0" encoding="utf-8"?>
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
<robot name="moveo_urdf">
  <link name="dummy">
  </link>
  <link name="base_link">
    <inertial>
      <origin xyz="-3.22852857881362E-06 0.00046899247310539 0.0707023084968957" rpy="0 0 0" />
      <mass value="2.57069193907154" />
      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
    </inertial>
    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
  </link>
  <link name="moveo_link1">
    <inertial>
      <origin xyz="0.000291566177196473 0.000104681575192028 0.0728057156146631" rpy="0 0 0" />
      <mass value="4.15952822957478" />
      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
    </inertial>
    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
  </link>
  <joint name="dummy_joint" type="fixed">
    <parent link="dummy"/>
    <child link="base_link"/>
  </joint>
  <joint name="moveo_joint1" type="continuous">
    <origin xyz="0 0 0.1715" rpy="0 0 0" />
    <parent link="base_link" />
    <child link="moveo_link1" />
    <axis xyz="0 0 1" />
    <limit lower="-3.14159" upper="3.14159" effort="10" velocity="100" />
  </joint>
  <link name="moveo_link2">
    <inertial>
      <origin xyz="-0.0011997332820832 6.4626035973292E-05 0.0828696520804673" rpy="0 0 0" />
      <mass value="1.84808635348241" />
      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
    </inertial>
    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
  </link>
  <joint name="moveo_joint2" type="revolute">
    <origin xyz="0 0 0.165" rpy="0 0 0" />
    <parent link="moveo_link1" />
    <child link="moveo_link2" />
    <axis xyz="-1 0 0" />
    <limit lower="-1" upper="2.15" effort="10" velocity="100" />
  </joint>
  <link name="moveo_link3">
    <inertial>
      <origin xyz="0.000651790401553304 -0.000105937403500567 0.0380190571919619" rpy="0 0 0" />
      <mass value="0.617310670458713" />
      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
    </inertial>
    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
  </link>
  <joint name="moveo_joint3" type="revolute">
    <origin xyz="0.001 0 0.22112" rpy="0 0 0" />
    <parent link="moveo_link2" />
    <child link="moveo_link3" />
    <axis xyz="-1 0 0" />
    <limit lower="0" upper="2.15" effort="10" velocity="100" />
  </joint>
  <link name="moveo_link4">
    <inertial>
      <origin xyz="-0.00620778315225003 2.10975020832893E-05 0.0531193403868238" rpy="0 0 0" />
      <mass value="0.346469873235588" />
      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
    </inertial>
    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
  </link>
  <joint name="moveo_joint4" type="revolute">
    <origin xyz="0 0 0.1275" rpy="0 0 0" />
    <parent link="moveo_link3" />
    <child link="moveo_link4" />
    <axis xyz="0 0 1" />
    <limit lower="-1.3745" upper="4.5161" effort="10" velocity="100" />
  </joint>
  <link name="moveo_link5">
    <inertial>
      <origin xyz="-0.000293805191189267 8.8360679328936E-09 0.00400995804790849" rpy="0 0 0" />
      <mass value="0.156134490708815" />
      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
    </inertial>
    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
  </link>
  <joint name="moveo_joint5" type="revolute">
    <origin xyz="0 -0.000135303178896679 0.0960000000083613" rpy="0 0 0" />
    <parent link="moveo_link4" />
    <child link="moveo_link5" />
    <axis xyz="-1 0 0" />
    <limit lower="-1.4677" upper="1.9495" effort="10" velocity="100" />
  </joint>
  <link name="moveo_nozzle_link">
    <inertial>
      <origin xyz="0.0107686264403774 -0.0325615730348289 0.0706687293479616" rpy="0 0 0" />
      <mass value="0.571607414496871" />
      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
    </inertial>
    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
  </link>
  <joint name="moveo_nozzle_joint" type="fixed">
    <origin xyz="-0.0109 -0.0386000000000001 0.1513" rpy="-3.14159265358979 0 0" />
    <parent link="moveo_link5" />
    <child link="moveo_nozzle_link" />
    <axis xyz="0 0 0" />
  </joint>
</robot>

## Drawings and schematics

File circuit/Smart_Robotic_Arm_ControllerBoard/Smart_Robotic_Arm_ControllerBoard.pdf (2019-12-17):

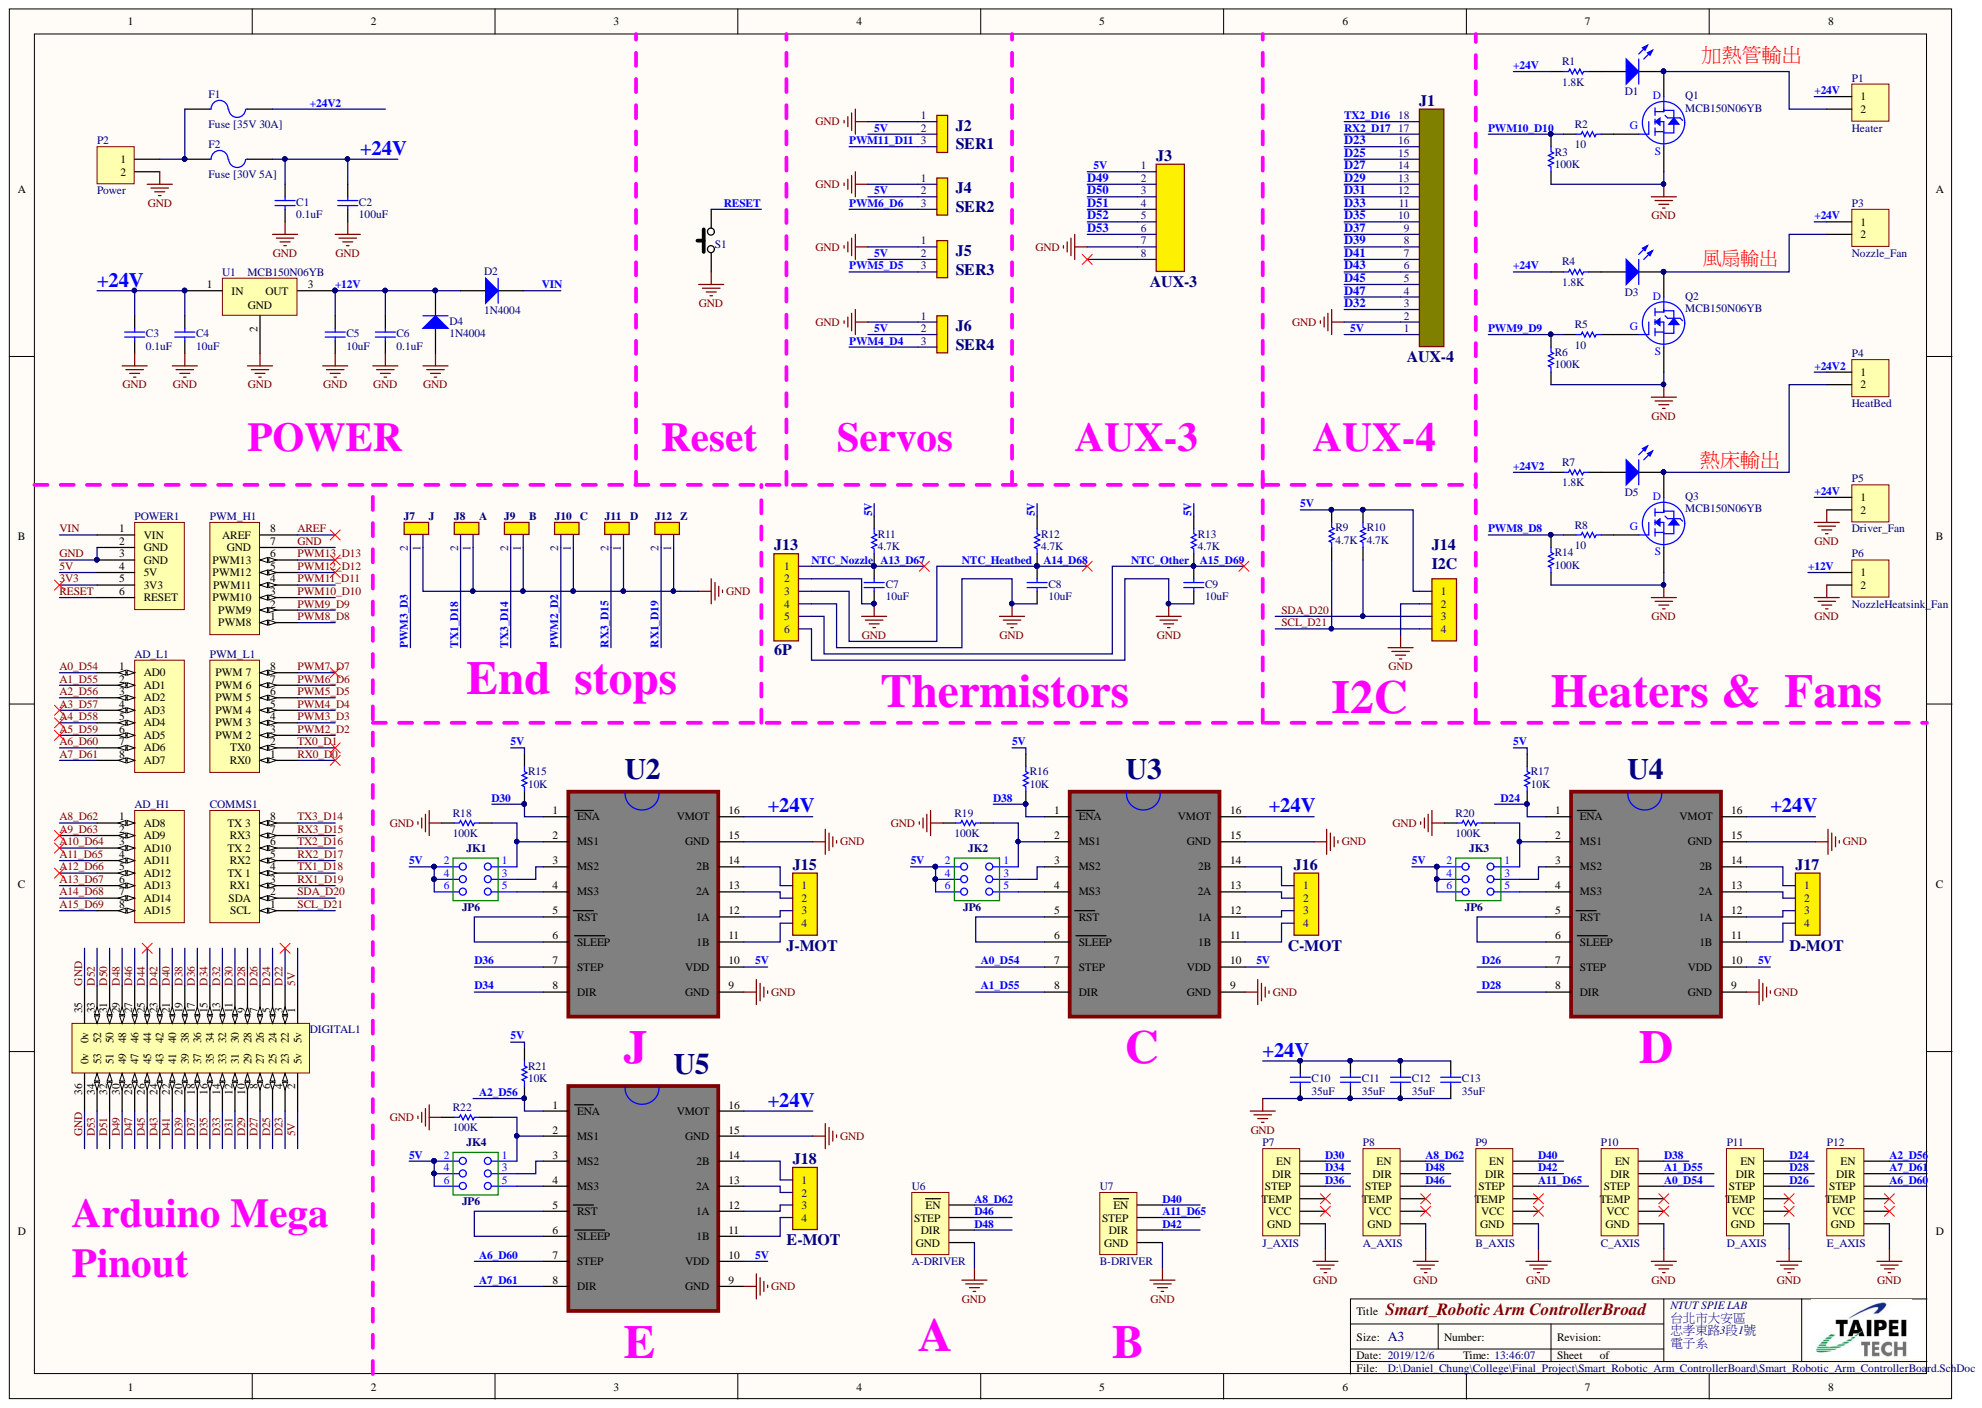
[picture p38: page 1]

Smart_Robotic Arm ControllerBroad Title | NTUT SPIE LAB 台北市大安區 忠孝東路3段1號 電子系

Size: A3 | Number: | Revision:
Date: 2019/12/6 Time: 13:46:07 | | Sheet of

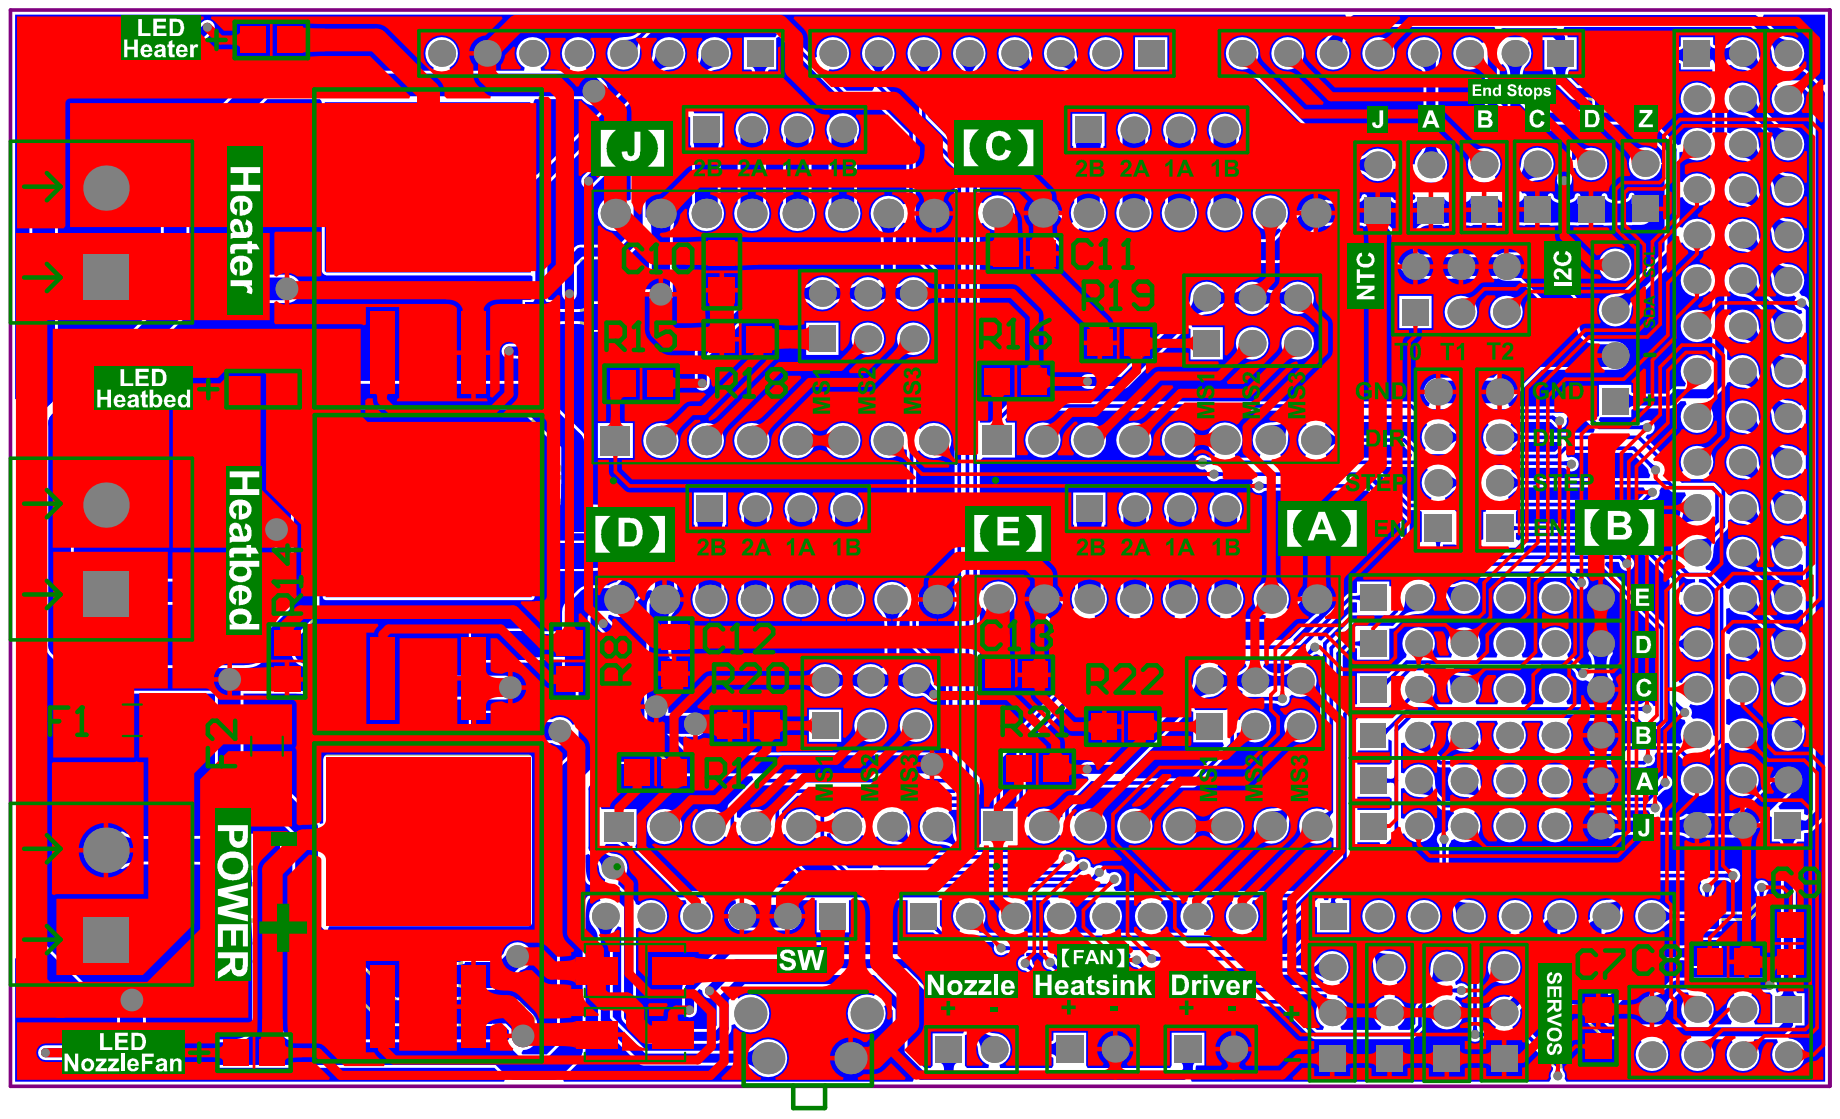
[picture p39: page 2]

Item # | Designator | Comment | Footprint | Quantity
1 | AD_H1 | AD_H | HDR1X8 | 1
2 | AD_L1 | AD_L | HDR1X8 | 1
3 | C1, C3, C6 | 0.1uF | SMD 0805 - CAP | 3
4 | C2 | 100uF | SMD 0805 - CAP | 1
5 | C4, C5, C7, C8, C9 | 10uF | SMD 0805 - CAP | 5
6 | C10, C11, C12, C13 | 35uF | SMD 0805 - CAP | 4
7 | COMMS1 | Communication | HDR1X8 | 1
8 | D1, D3, D5 | LED | SMD 0805 - LED | 3
9 | D2, D4 | 1N4004 | DO-214AC | 2
10 | DIGITAL1 | IO_36 | HDR2X18 | 1
11 | F1 | Fuse [35V 30A] | SMD 1206 | 1
12 | F2 | Fuse [30V 5A] | SMD 1206 | 1
13 | J1 | AUX-4 | HDR1X18 | 1
14 | J2 | SER1 | HDR1X3 | 1
15 | J3 | AUX-3 | HDR2X4 | 1
16 | J4 | SER2 | HDR1X3 | 1
17 | J5 | SER3 | HDR1X3 | 1
18 | J6 | SER4 | HDR1X3 | 1
19 | J7 | J | HDR1X2 | 1
20 | J8 | A | HDR1X2 | 1
21 | J9 | B | HDR1X2 | 1
22 | J10 | C | HDR1X2 | 1
23 | J11 | D | HDR1X2 | 1
24 | J12 | Z | HDR1X2 | 1
25 | J13 | 6P | HDR2X3 | 1
26 | J14 | I2C | HDR1X4 | 1
27 | J15 | J-MOT | HDR1X4 | 1
28 | J16 | C-MOT | HDR1X4 | 1
29 | J17 | D-MOT | HDR1X4 | 1
30 | J18 | E-MOT | HDR1X4 | 1
31 | JK1, JK2, JK3, JK4 | JP6 | HDR2X3 | 4
32 | P1 | Heater | HDR1X2 - 5mm | 1
33 | P2 | Power | HDR1X2 - 5mm | 1
34 | P3 | Nozzle_Fan | HDR1X2 | 1
35 | P4 | HeatBed | HDR1X2 - 5mm | 1
36 | P5 | Driver_Fan | HDR1X2 | 1
37 | P6 | NozzleHeatsink_Fan | HDR1X2 | 1
38 | P7 | J_AXIS | HDR1X6 | 1
39 | P8 | A_AXIS | HDR1X6 | 1
40 | P9 | B_AXIS | HDR1X6 | 1
41 | P10 | C_AXIS | HDR1X6 | 1
42 | P11 | D_AXIS | HDR1X6 | 1
43 | P12 | E_AXIS | HDR1X6 | 1
44 | POWER1 | POWER | HDR1X6 | 1
45 | PWM_H1 | PWM_H | HDR1X8 | 1
46 | PWM_L1 | PWM_L | HDR1X8 | 1
47 | Q1, Q2, Q3 | MCB150N06YB | TO-263-2 | 3
48 | R1, R2, R3, R4, R5, R6, R7, R8, R9, R10, R11, R12, R13, R14, R15, R16, R17, R18, R19, R20, R21, R22 | R1 | SMD 0805 - RES | 22
49 | S1 | SW | SW2 | 1
50 | U1 | MCB150N06YB | TO-252-3 | 1
51 | U2, U3, U4, U5 | | Stepper driver Broad | 4
52 | U6 | A-DRIVER | HDR1X4 | 1
53 | U7 | B-DRIVER | HDR1X4 | 1

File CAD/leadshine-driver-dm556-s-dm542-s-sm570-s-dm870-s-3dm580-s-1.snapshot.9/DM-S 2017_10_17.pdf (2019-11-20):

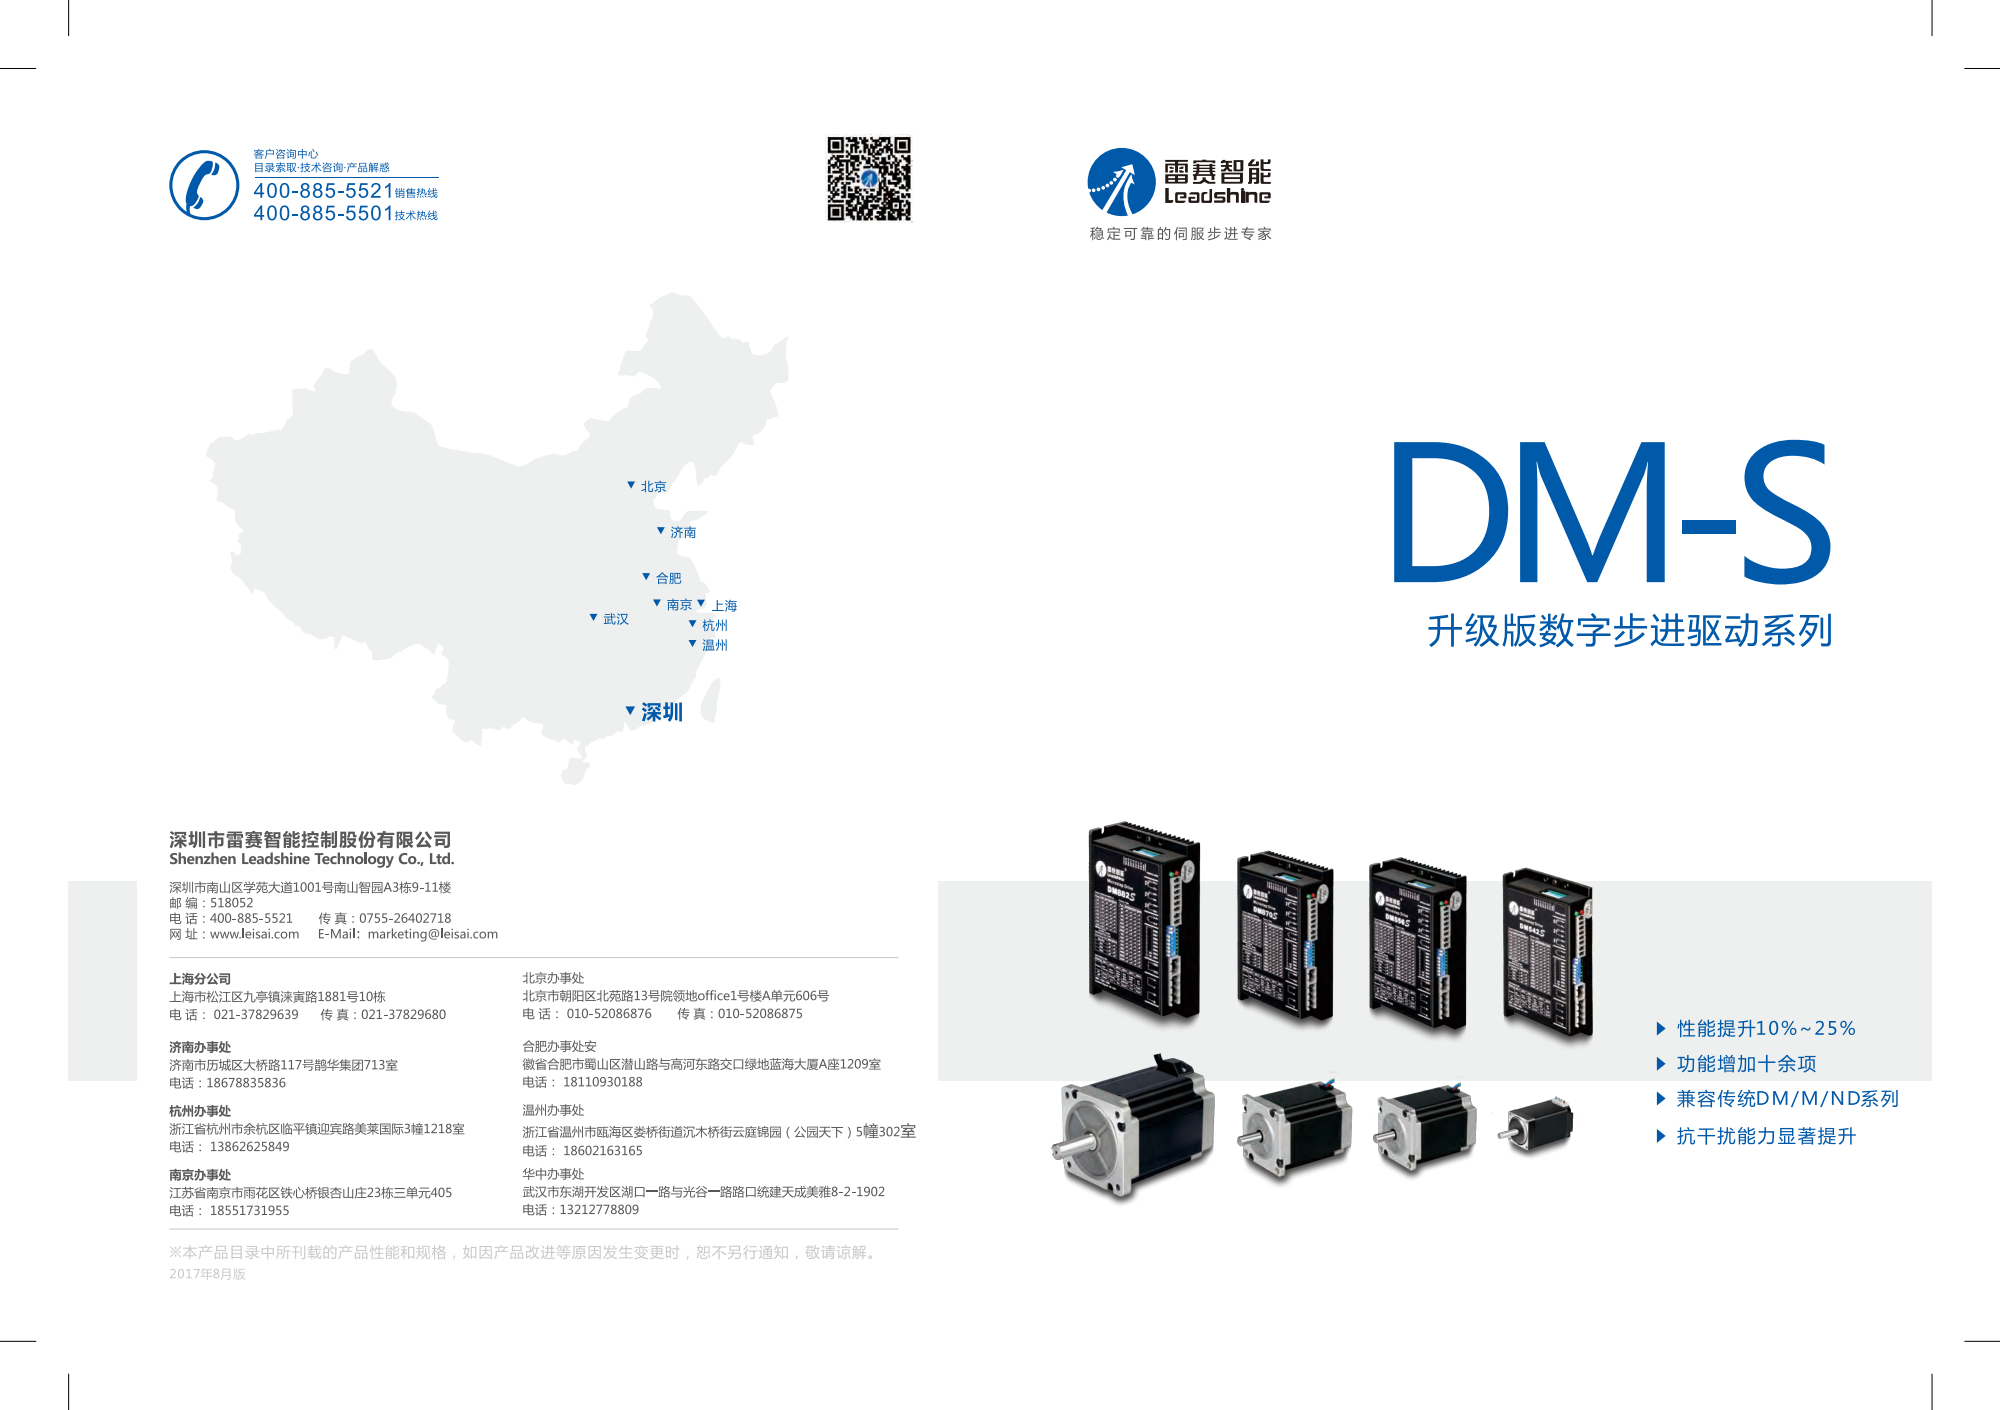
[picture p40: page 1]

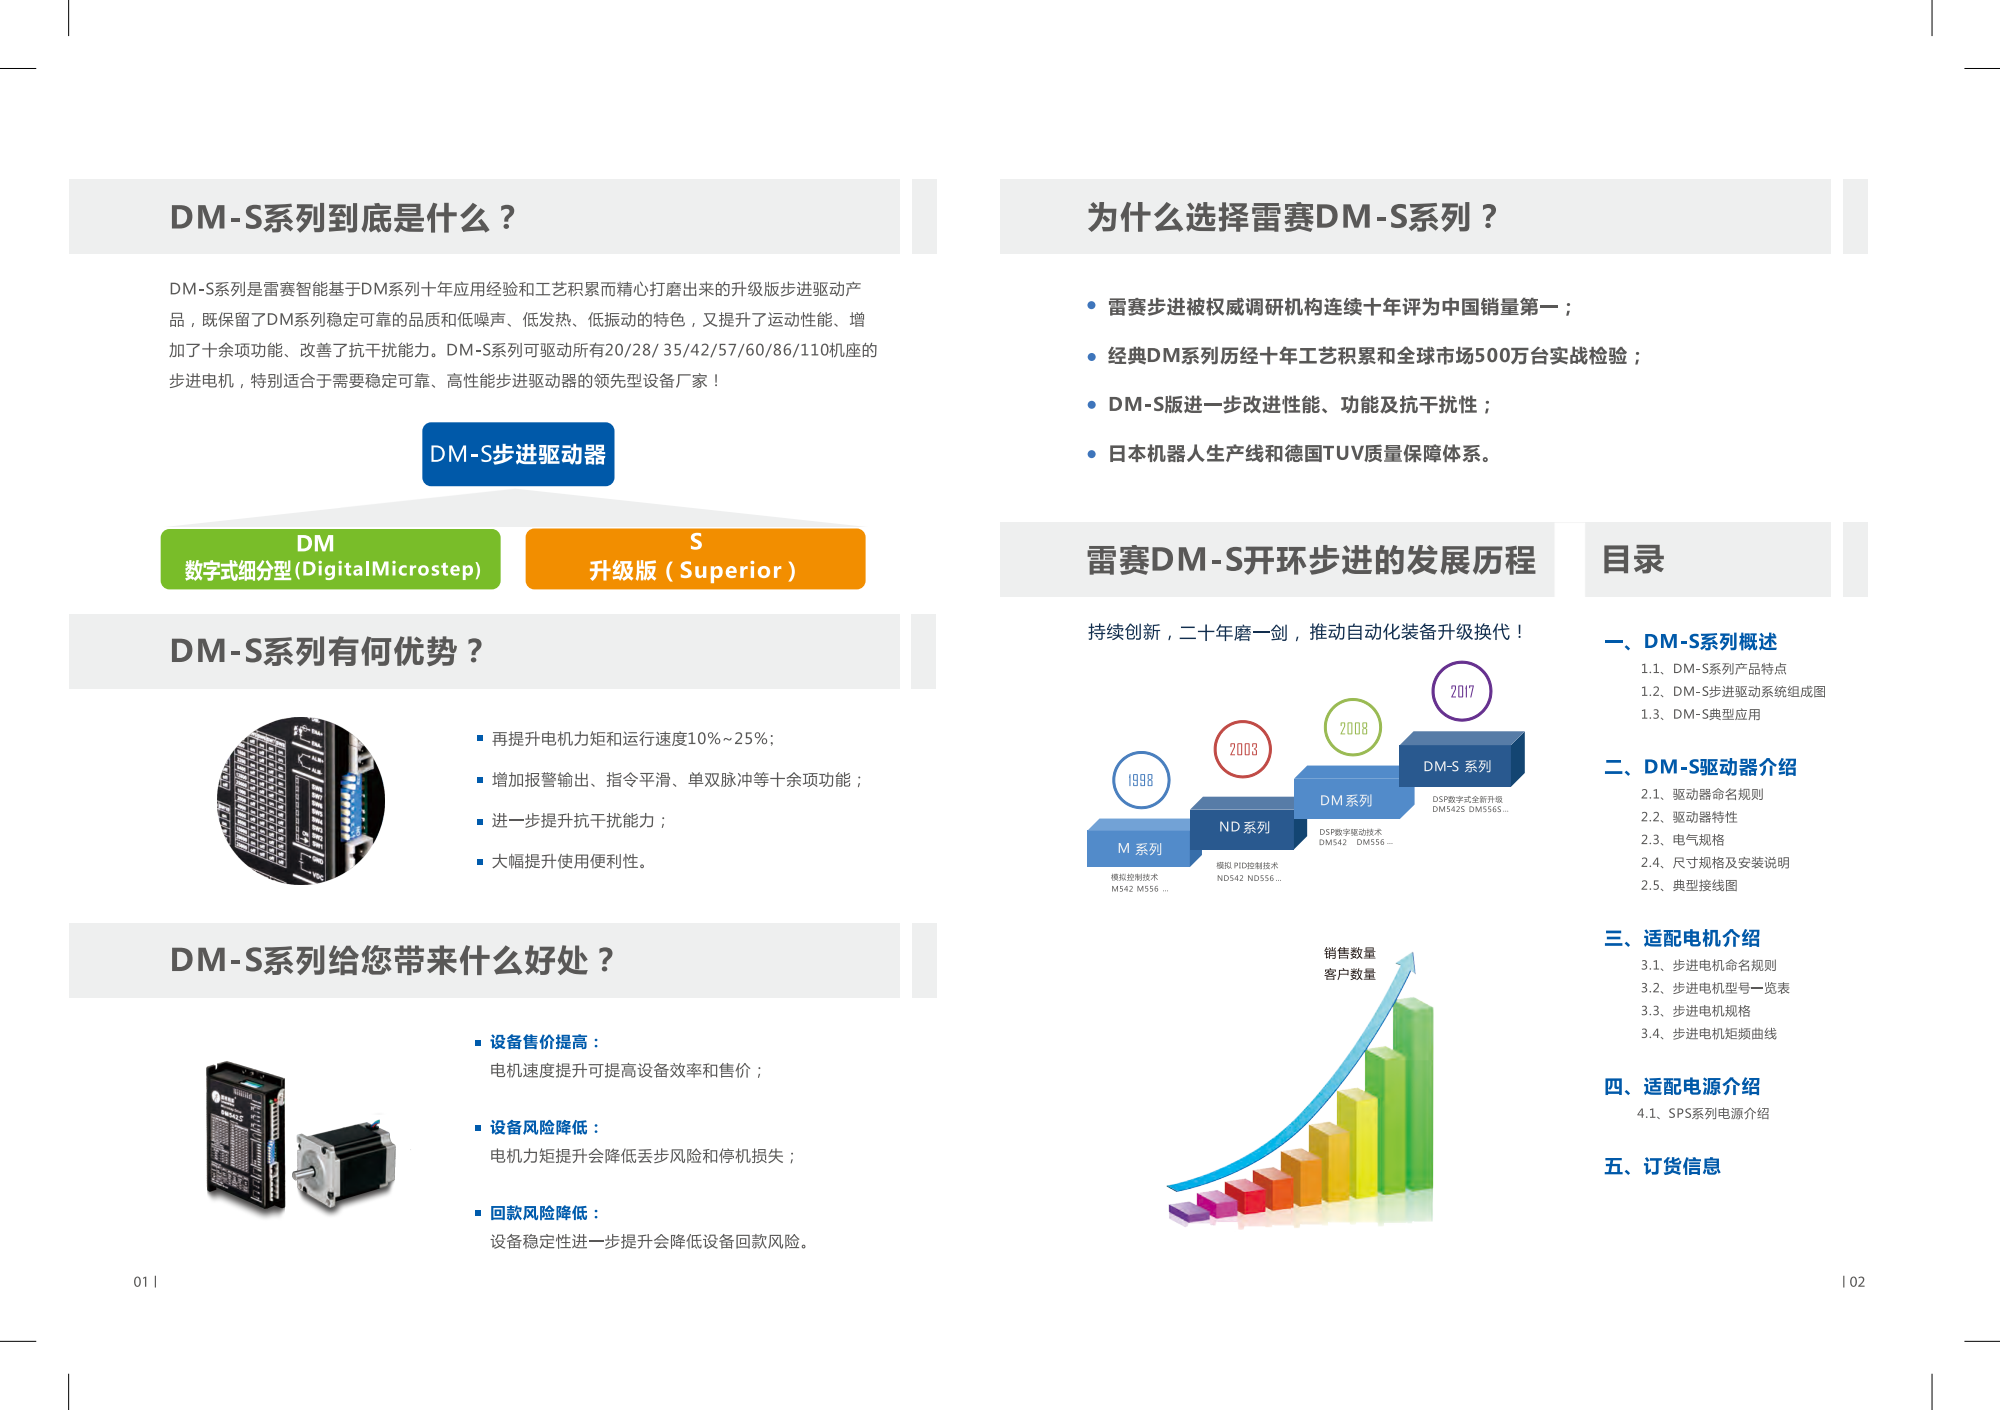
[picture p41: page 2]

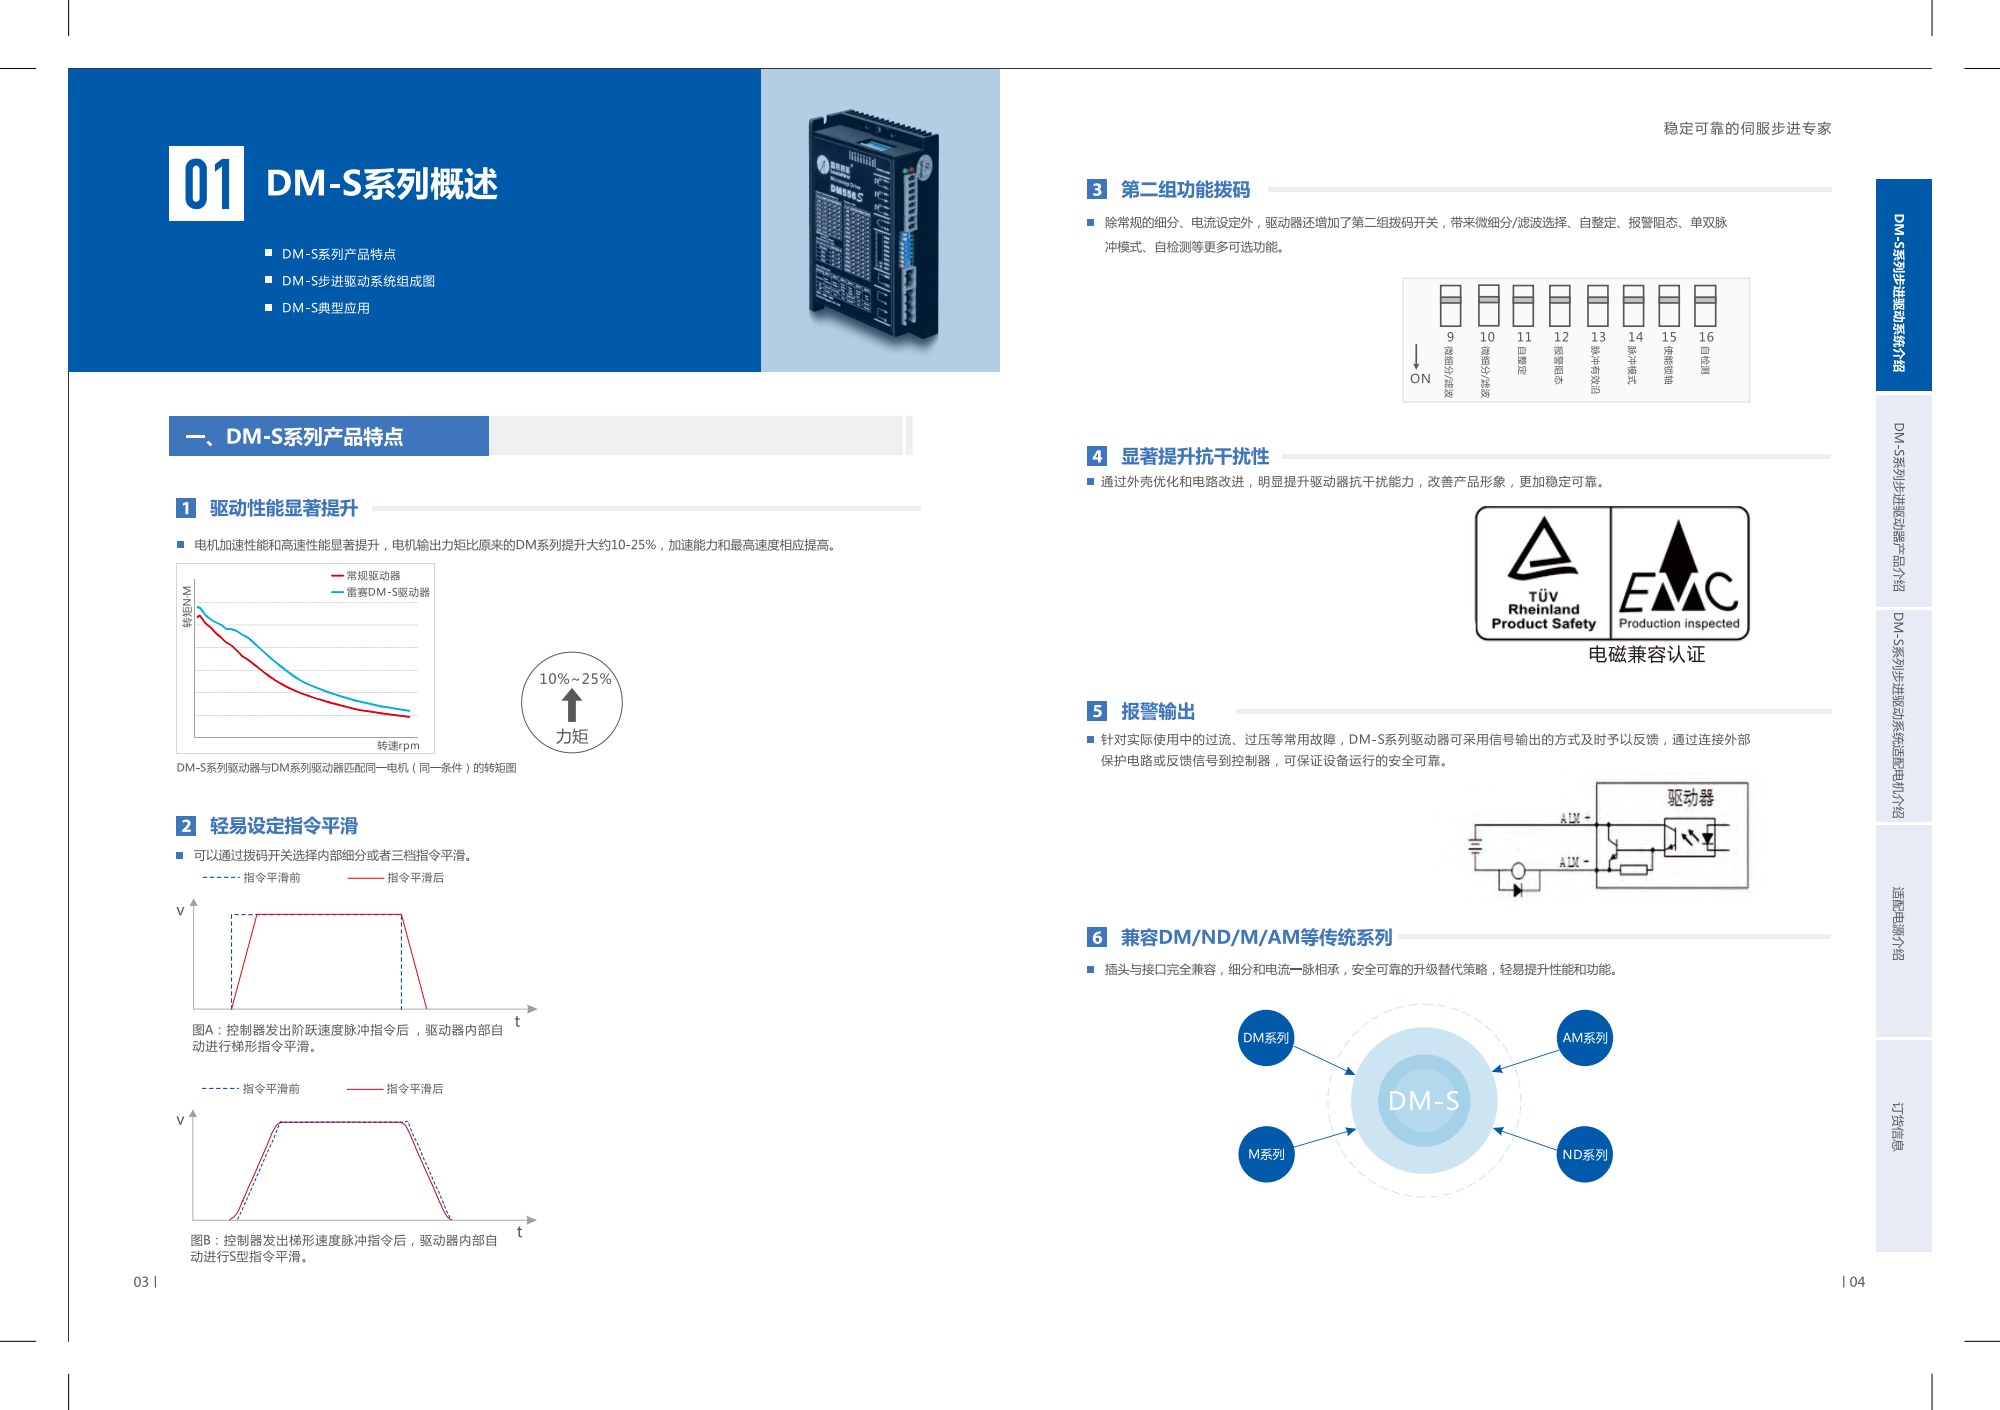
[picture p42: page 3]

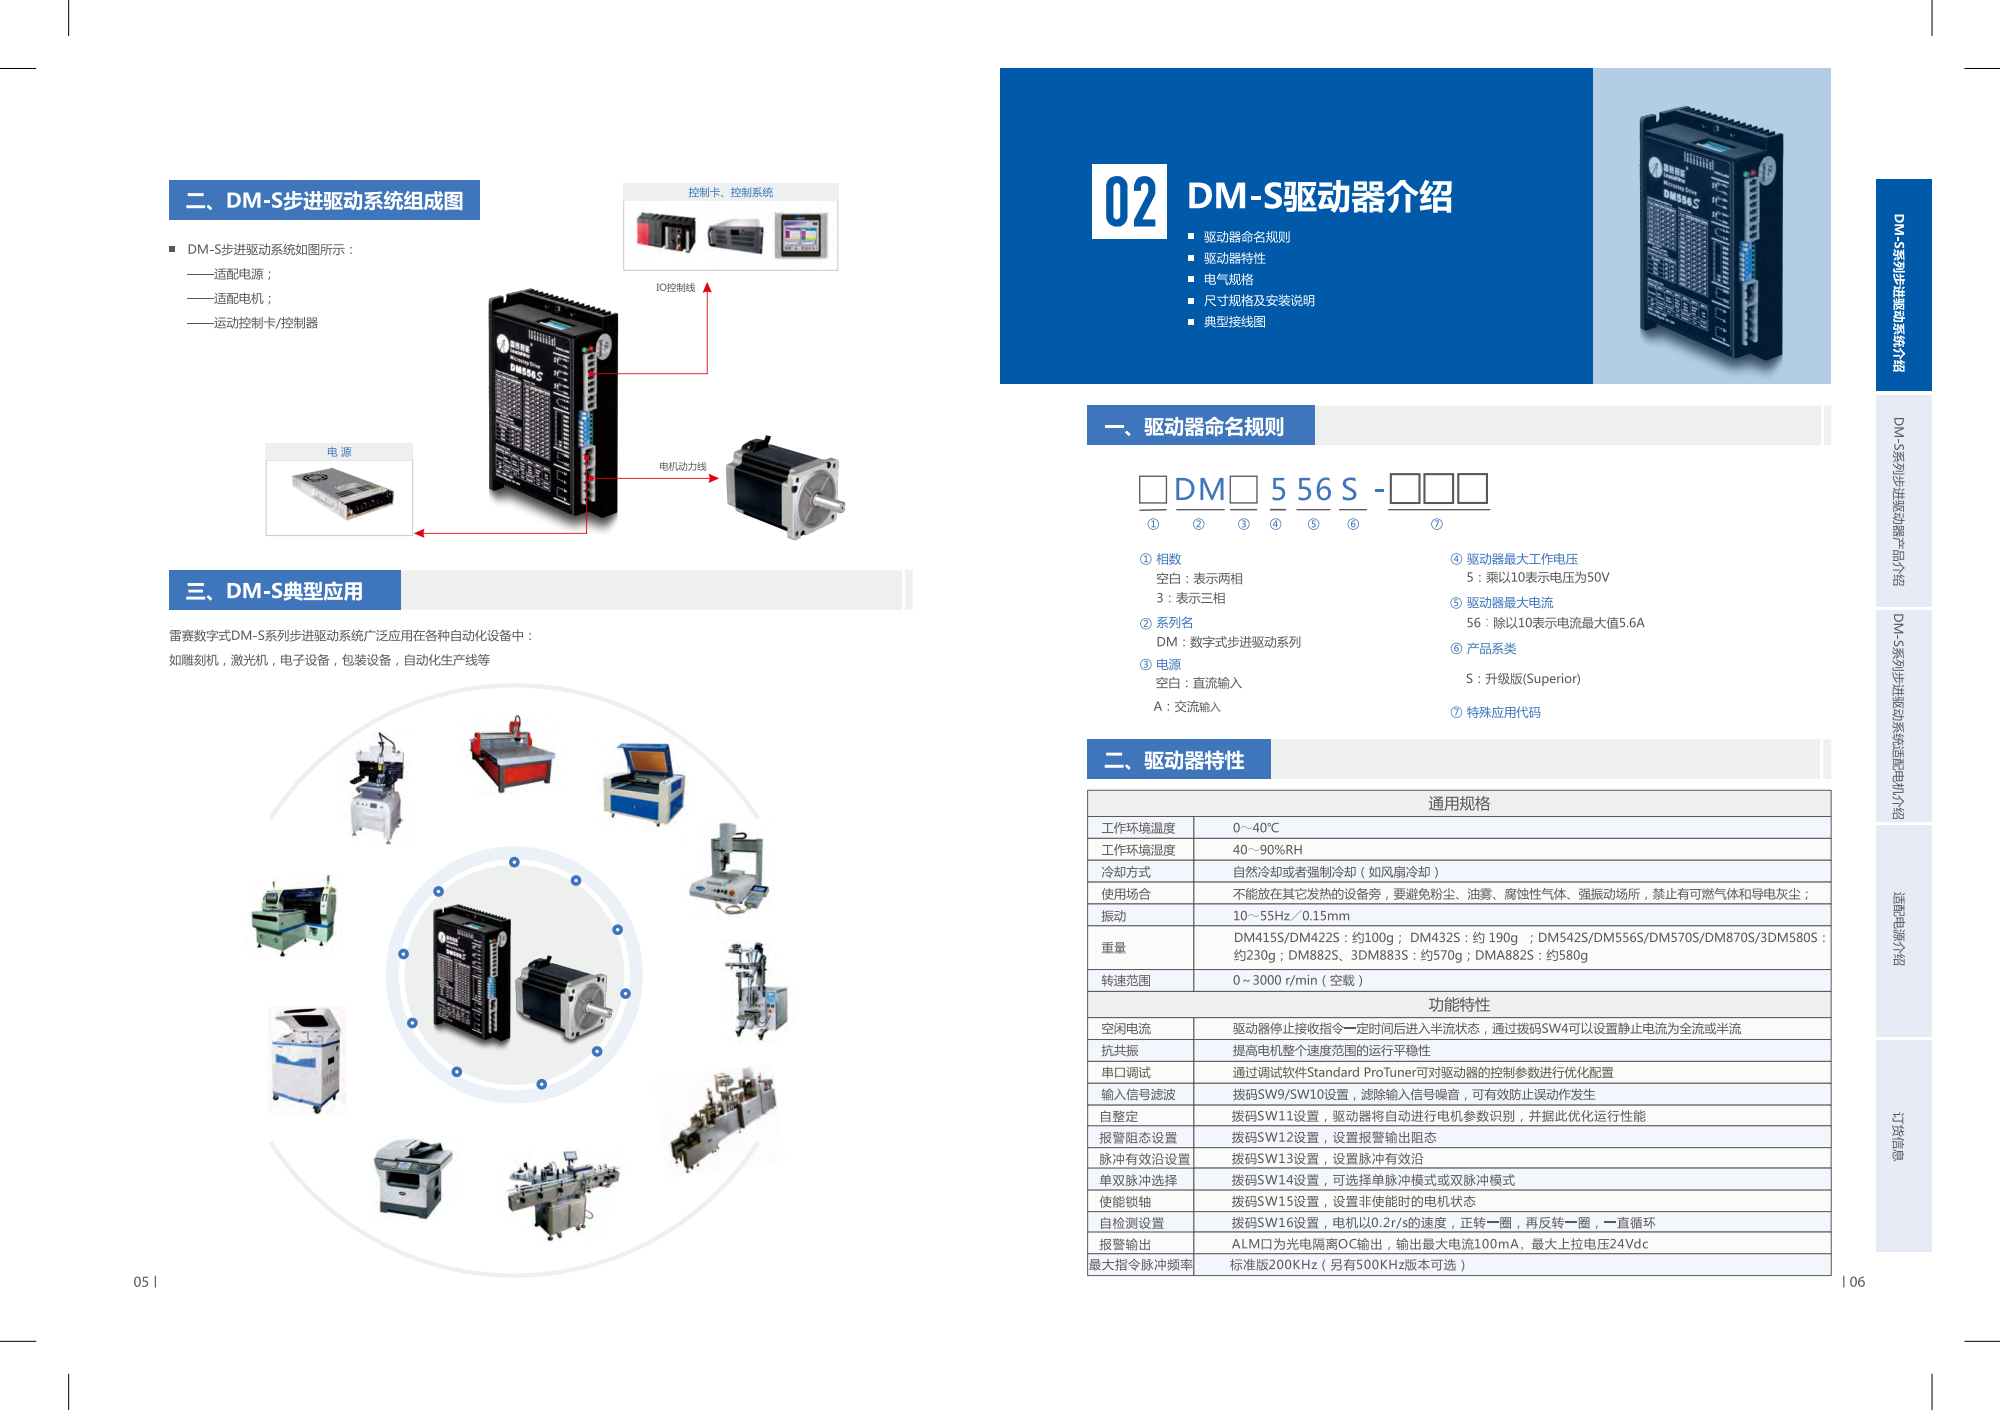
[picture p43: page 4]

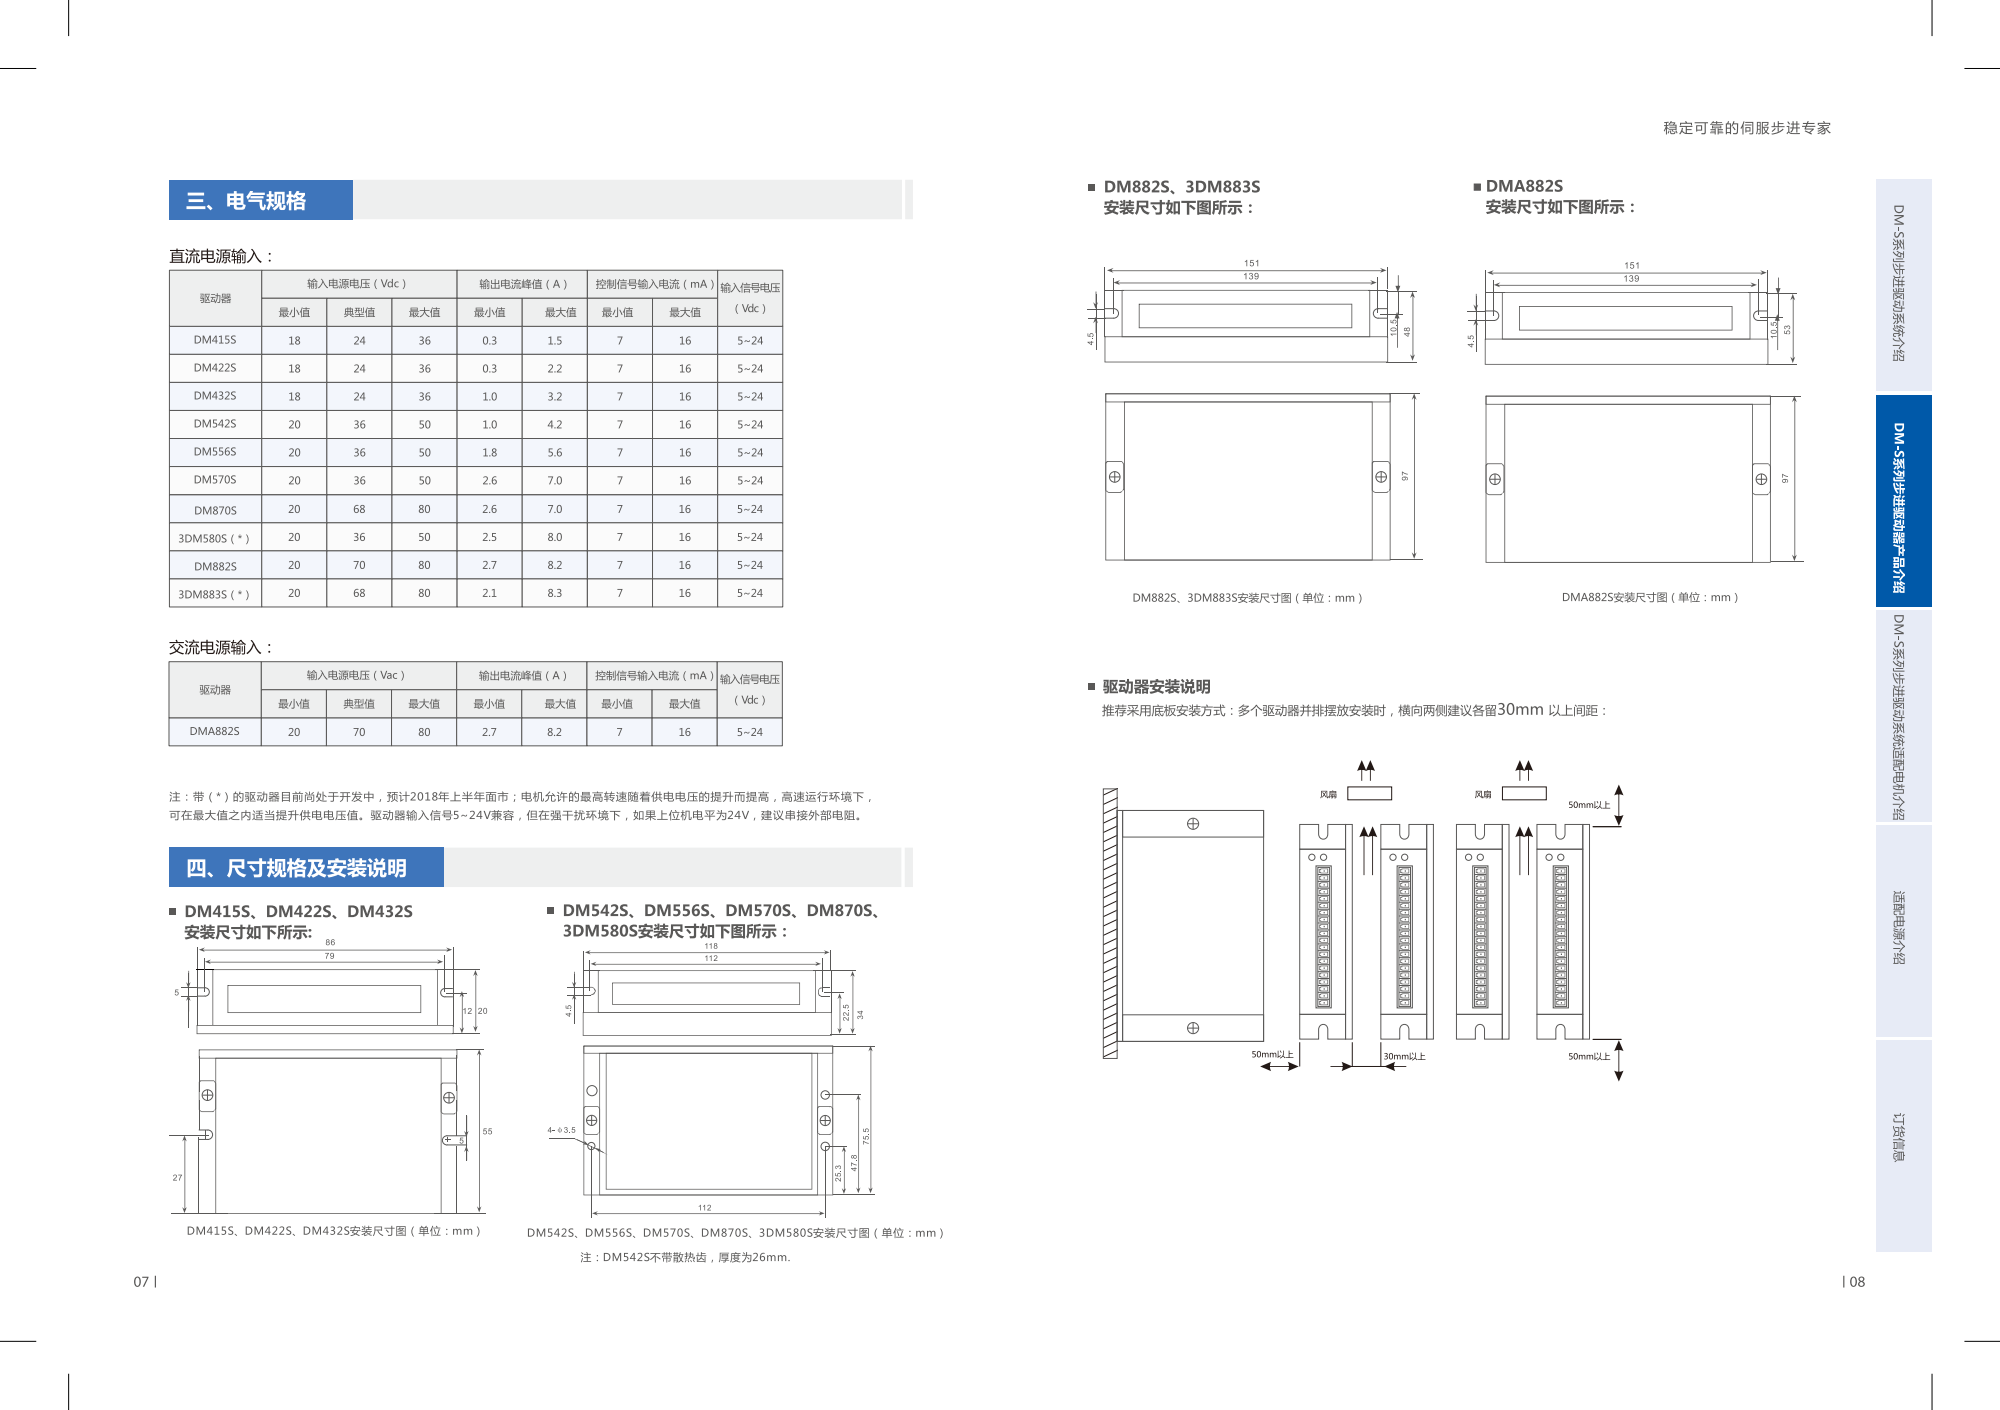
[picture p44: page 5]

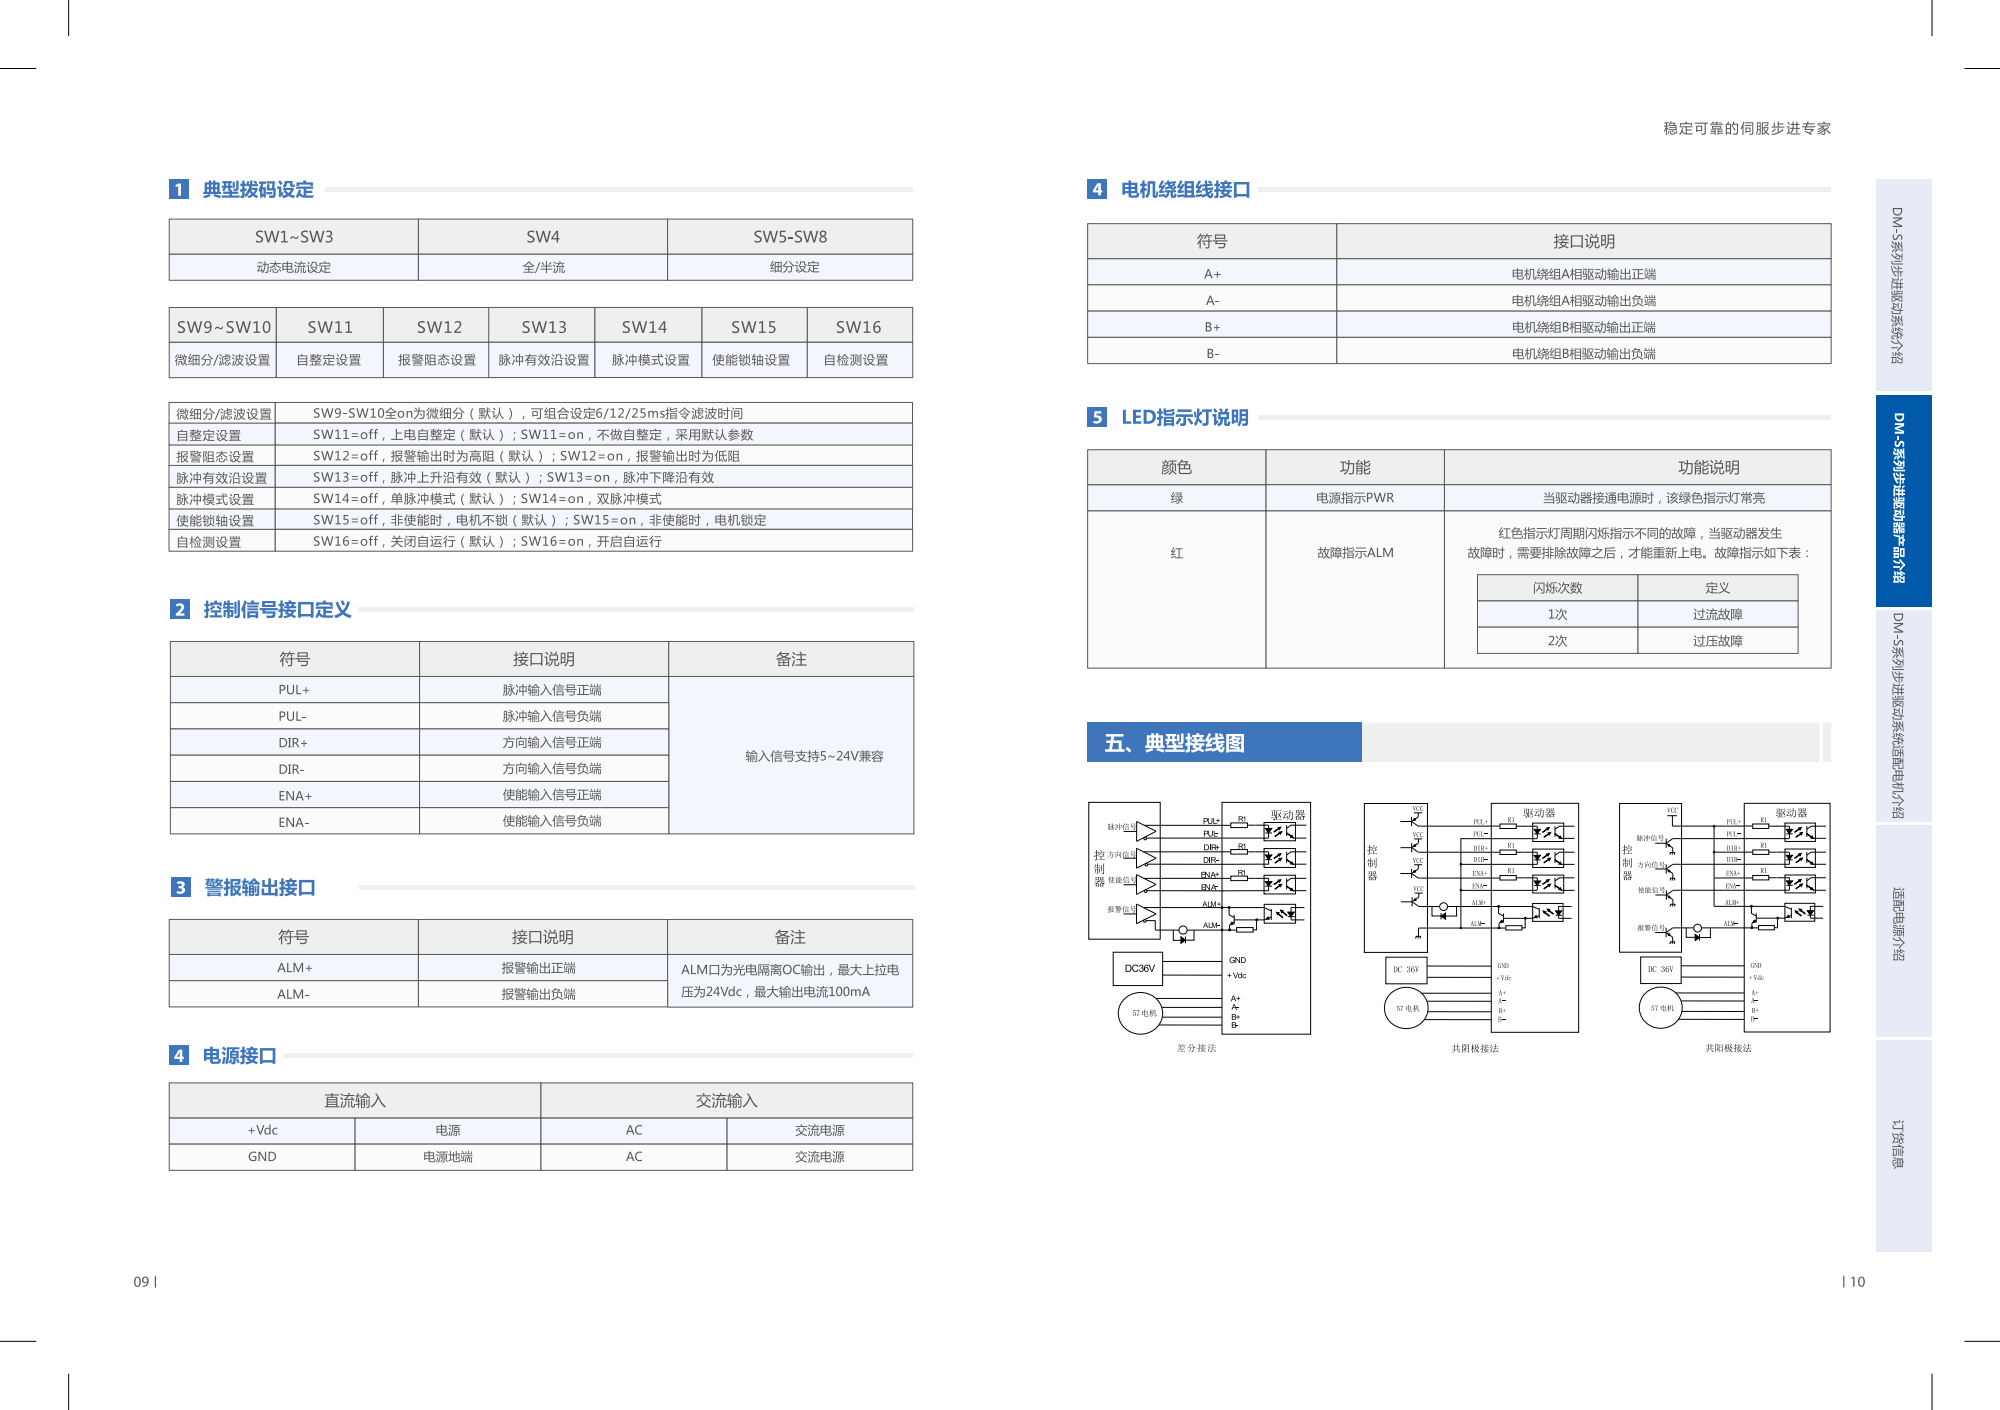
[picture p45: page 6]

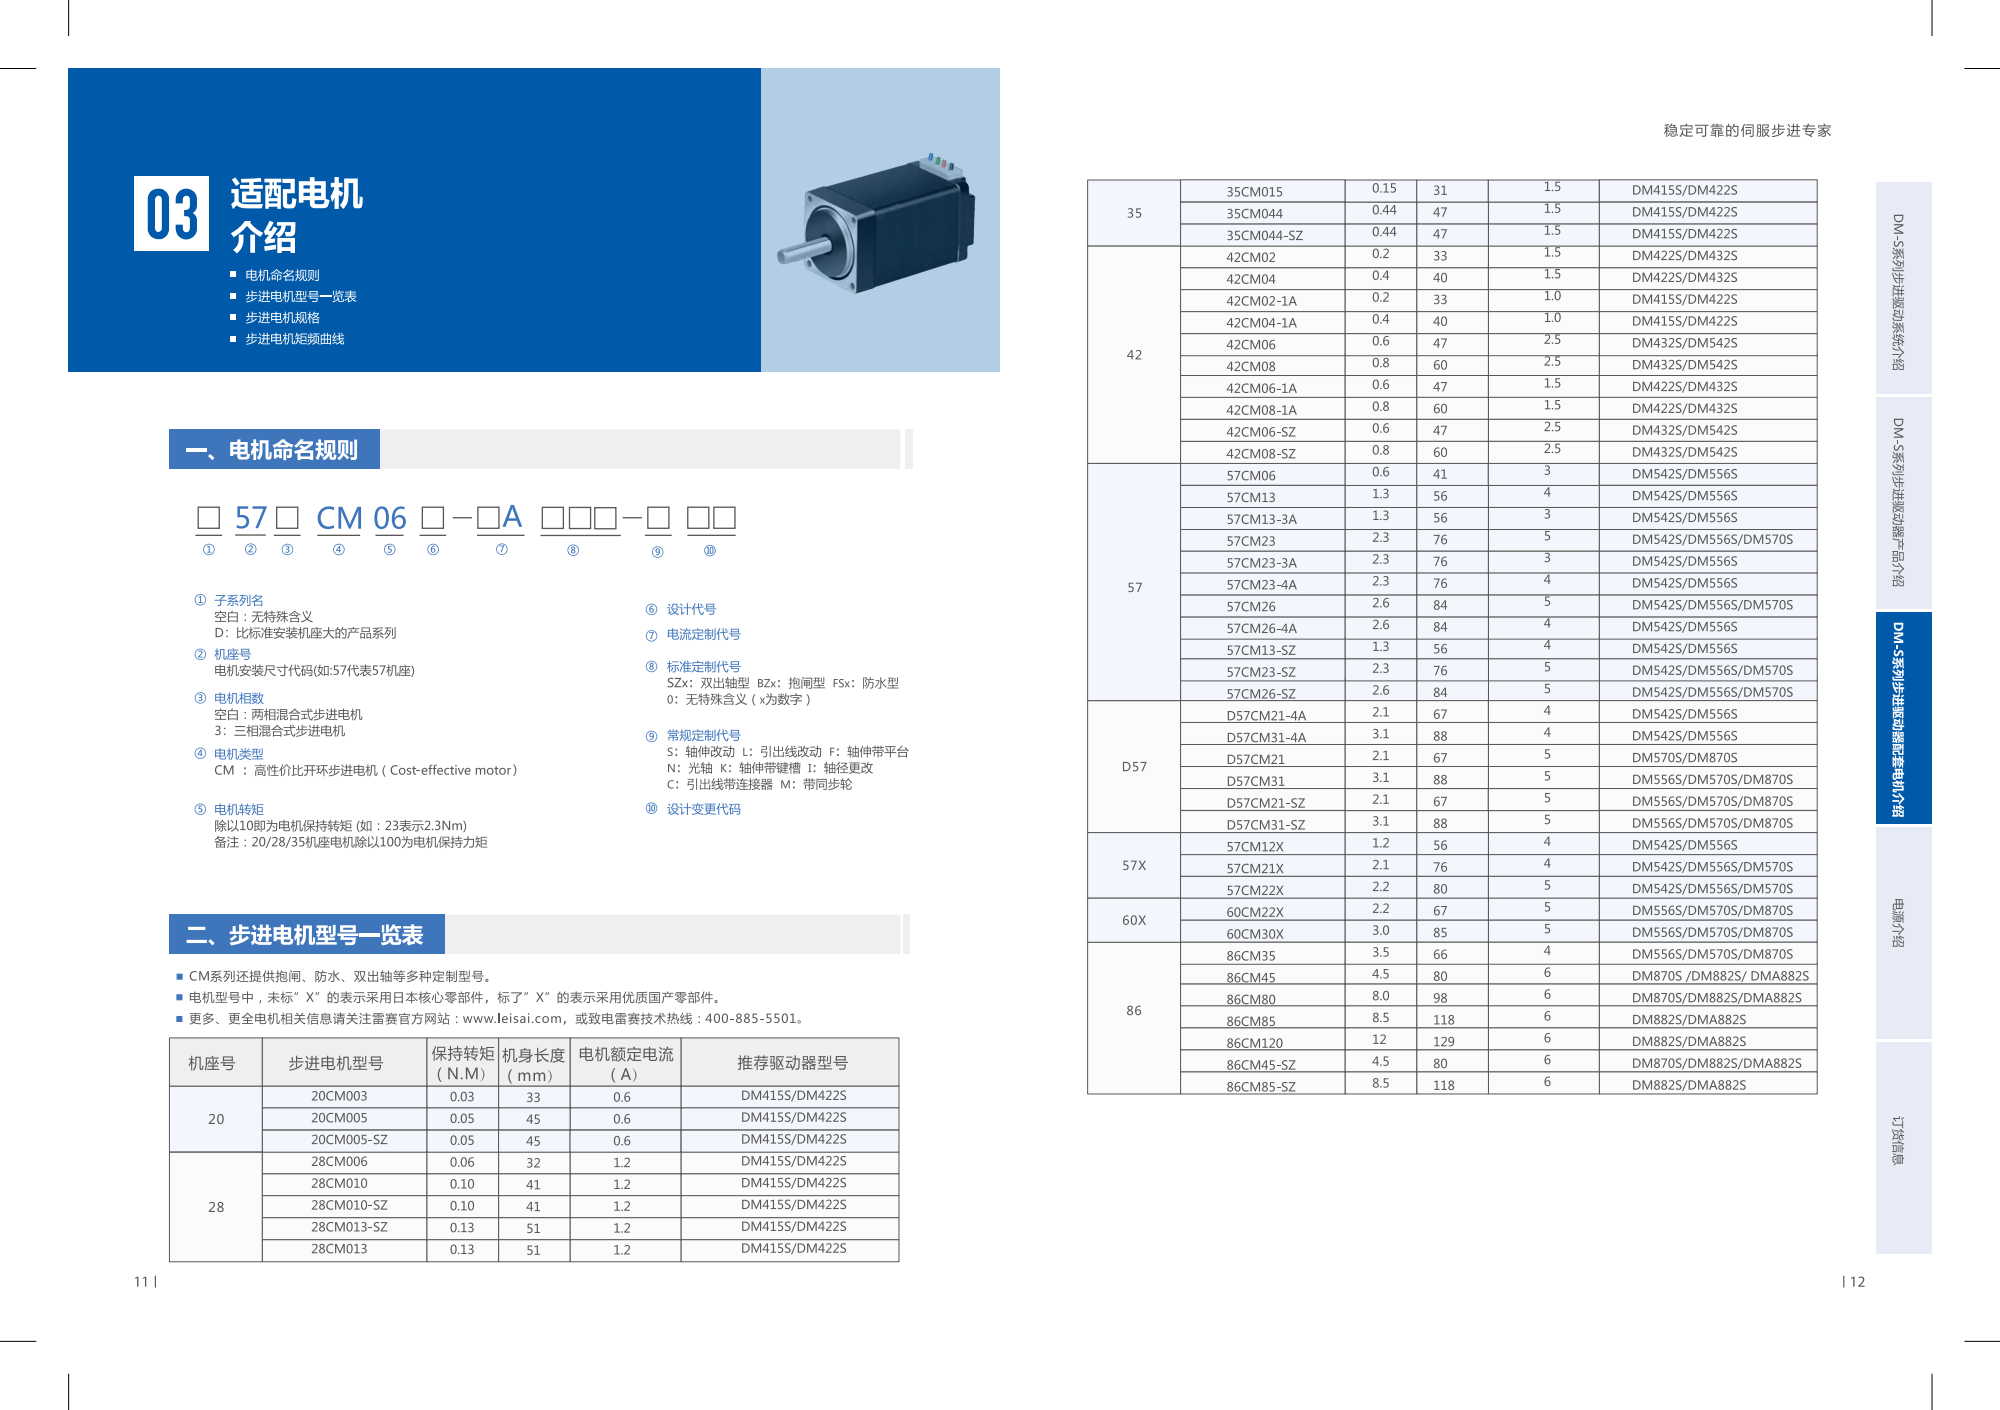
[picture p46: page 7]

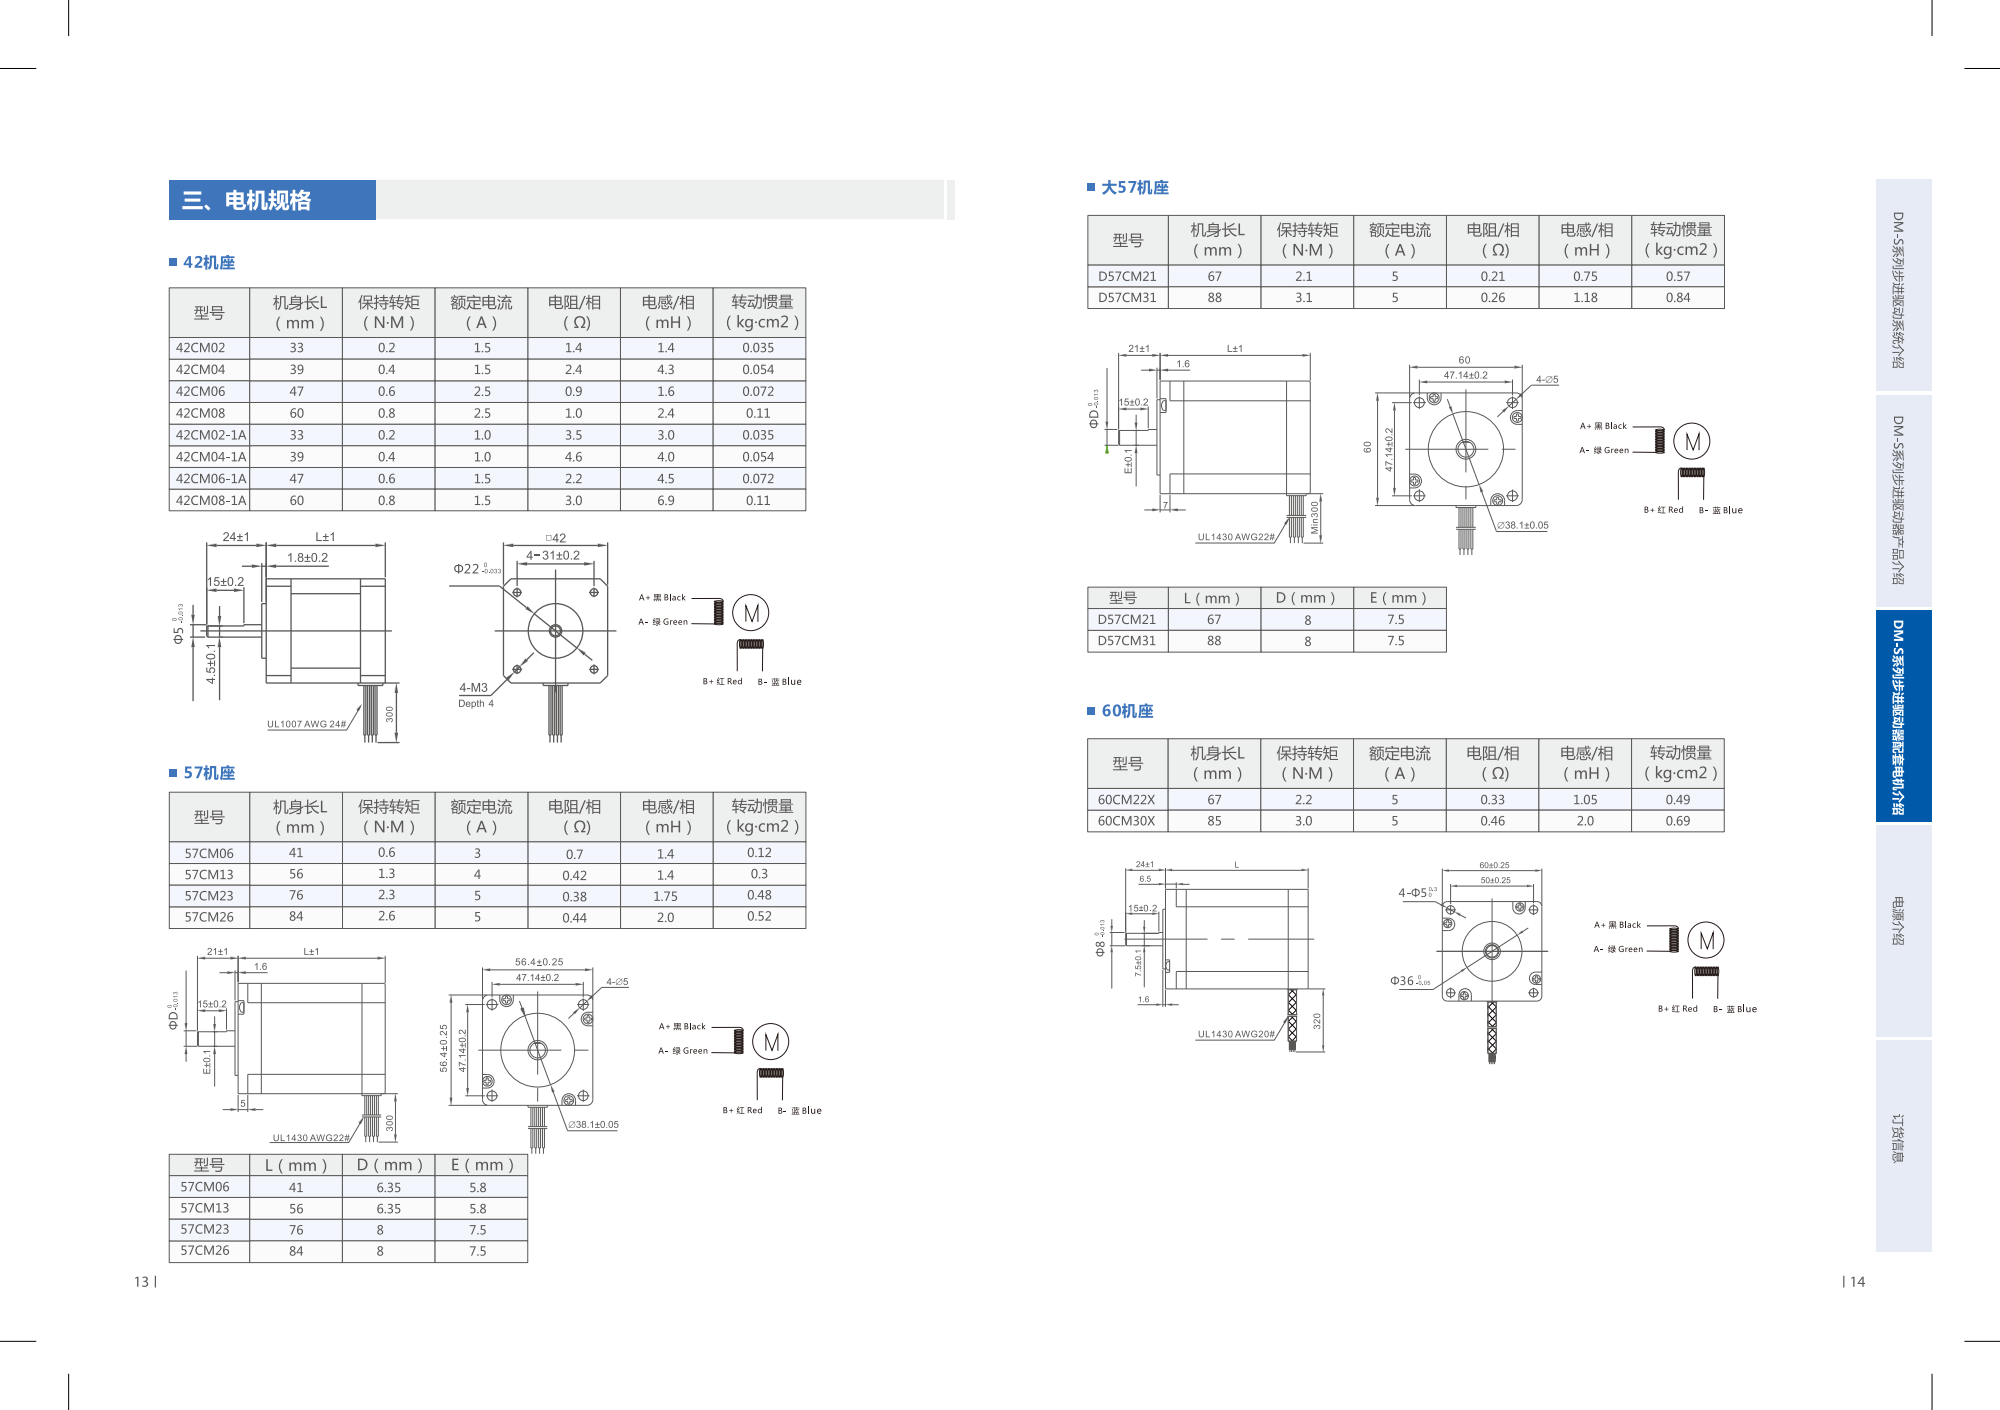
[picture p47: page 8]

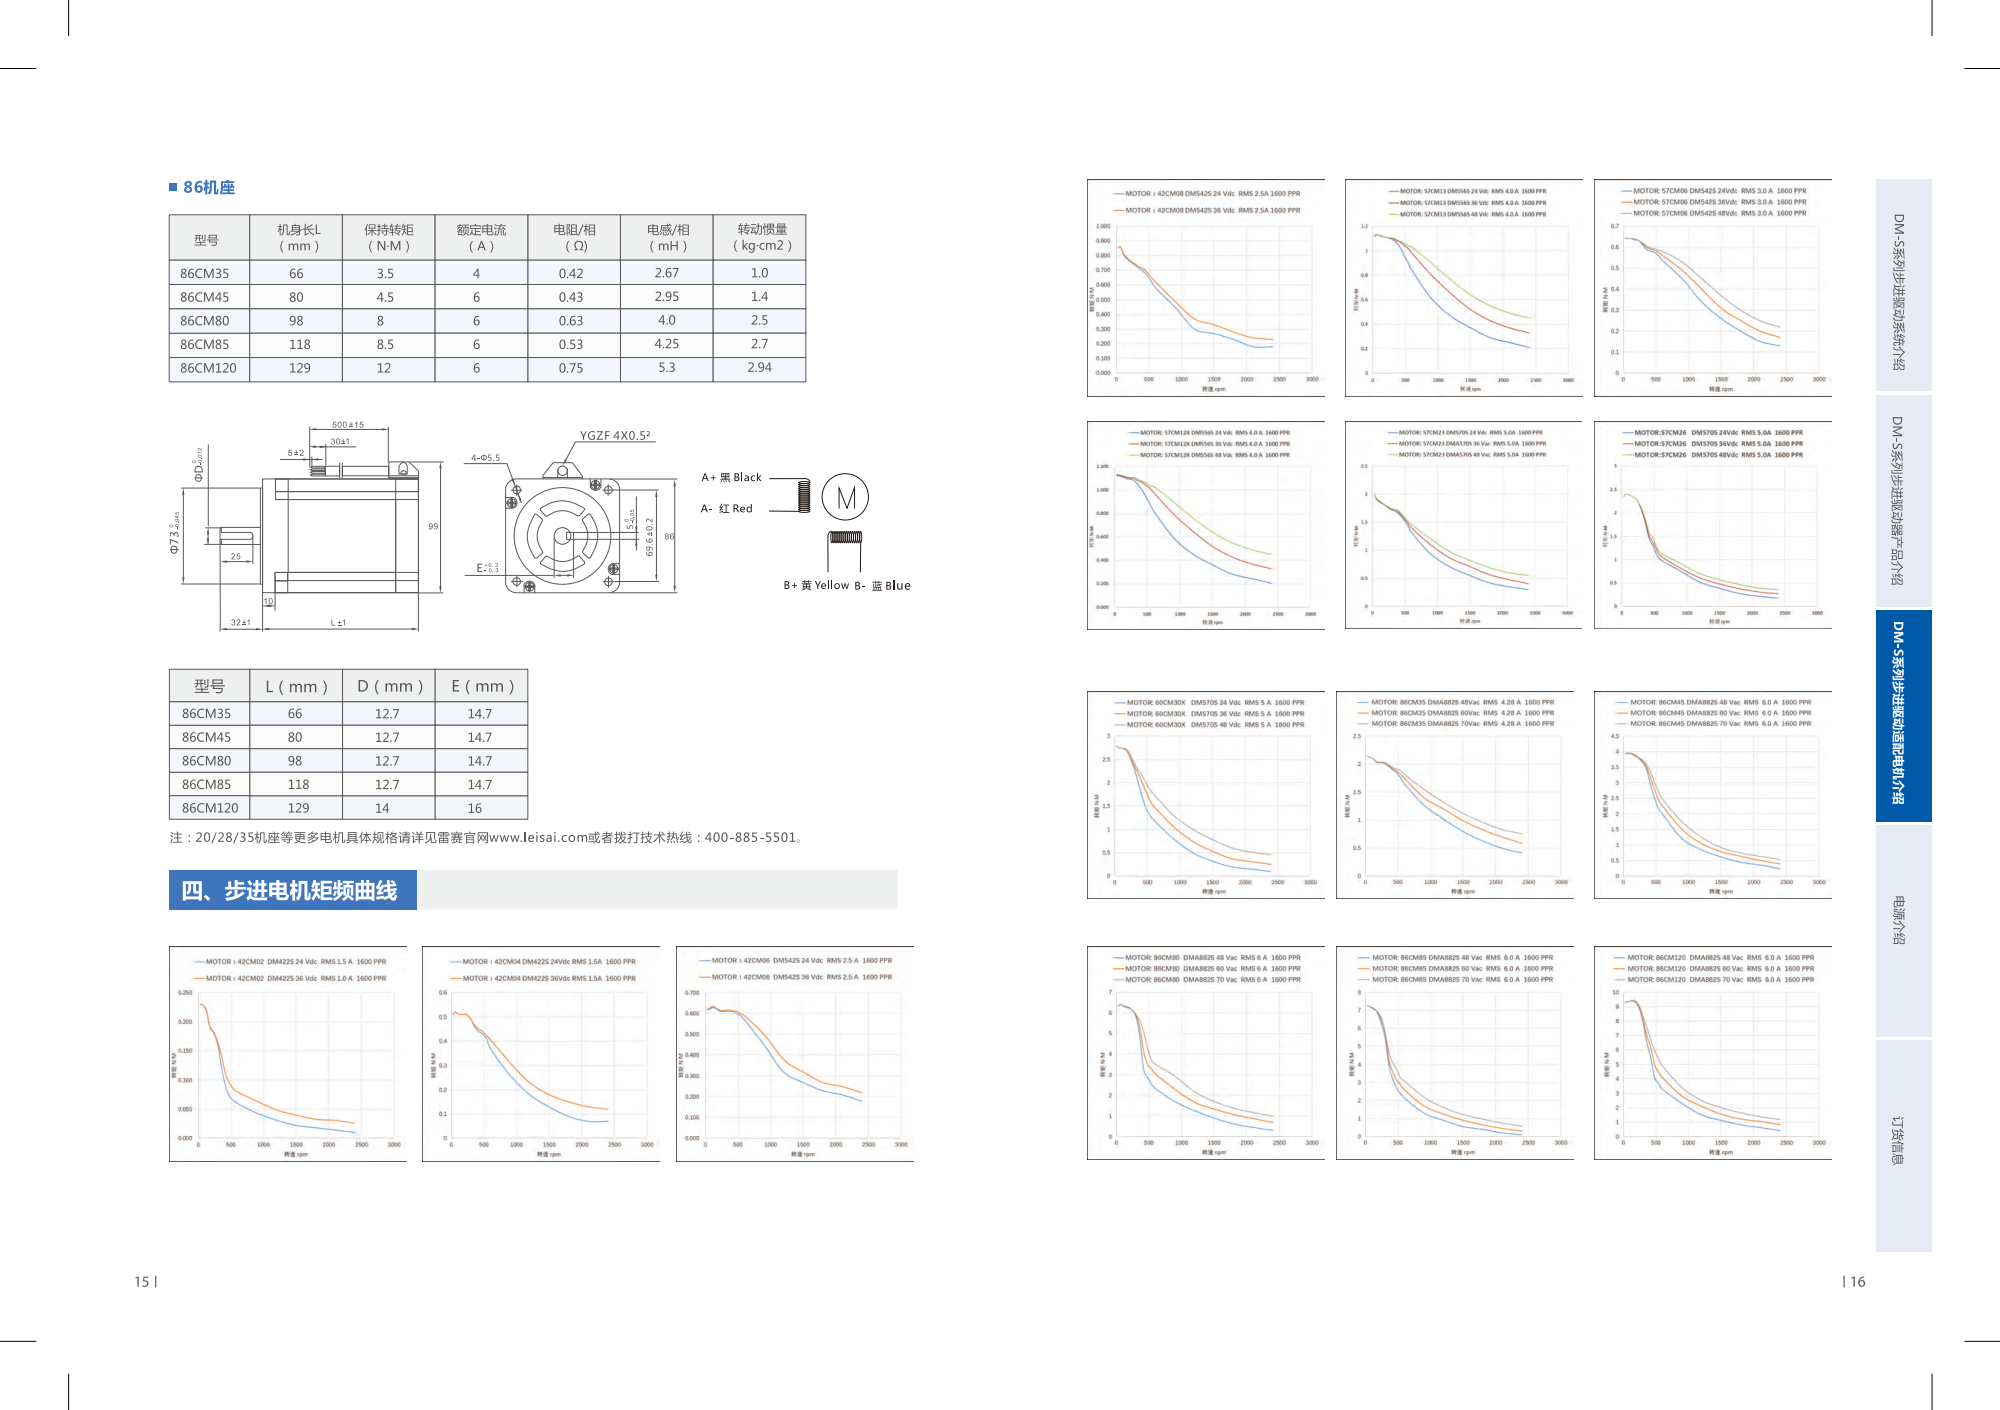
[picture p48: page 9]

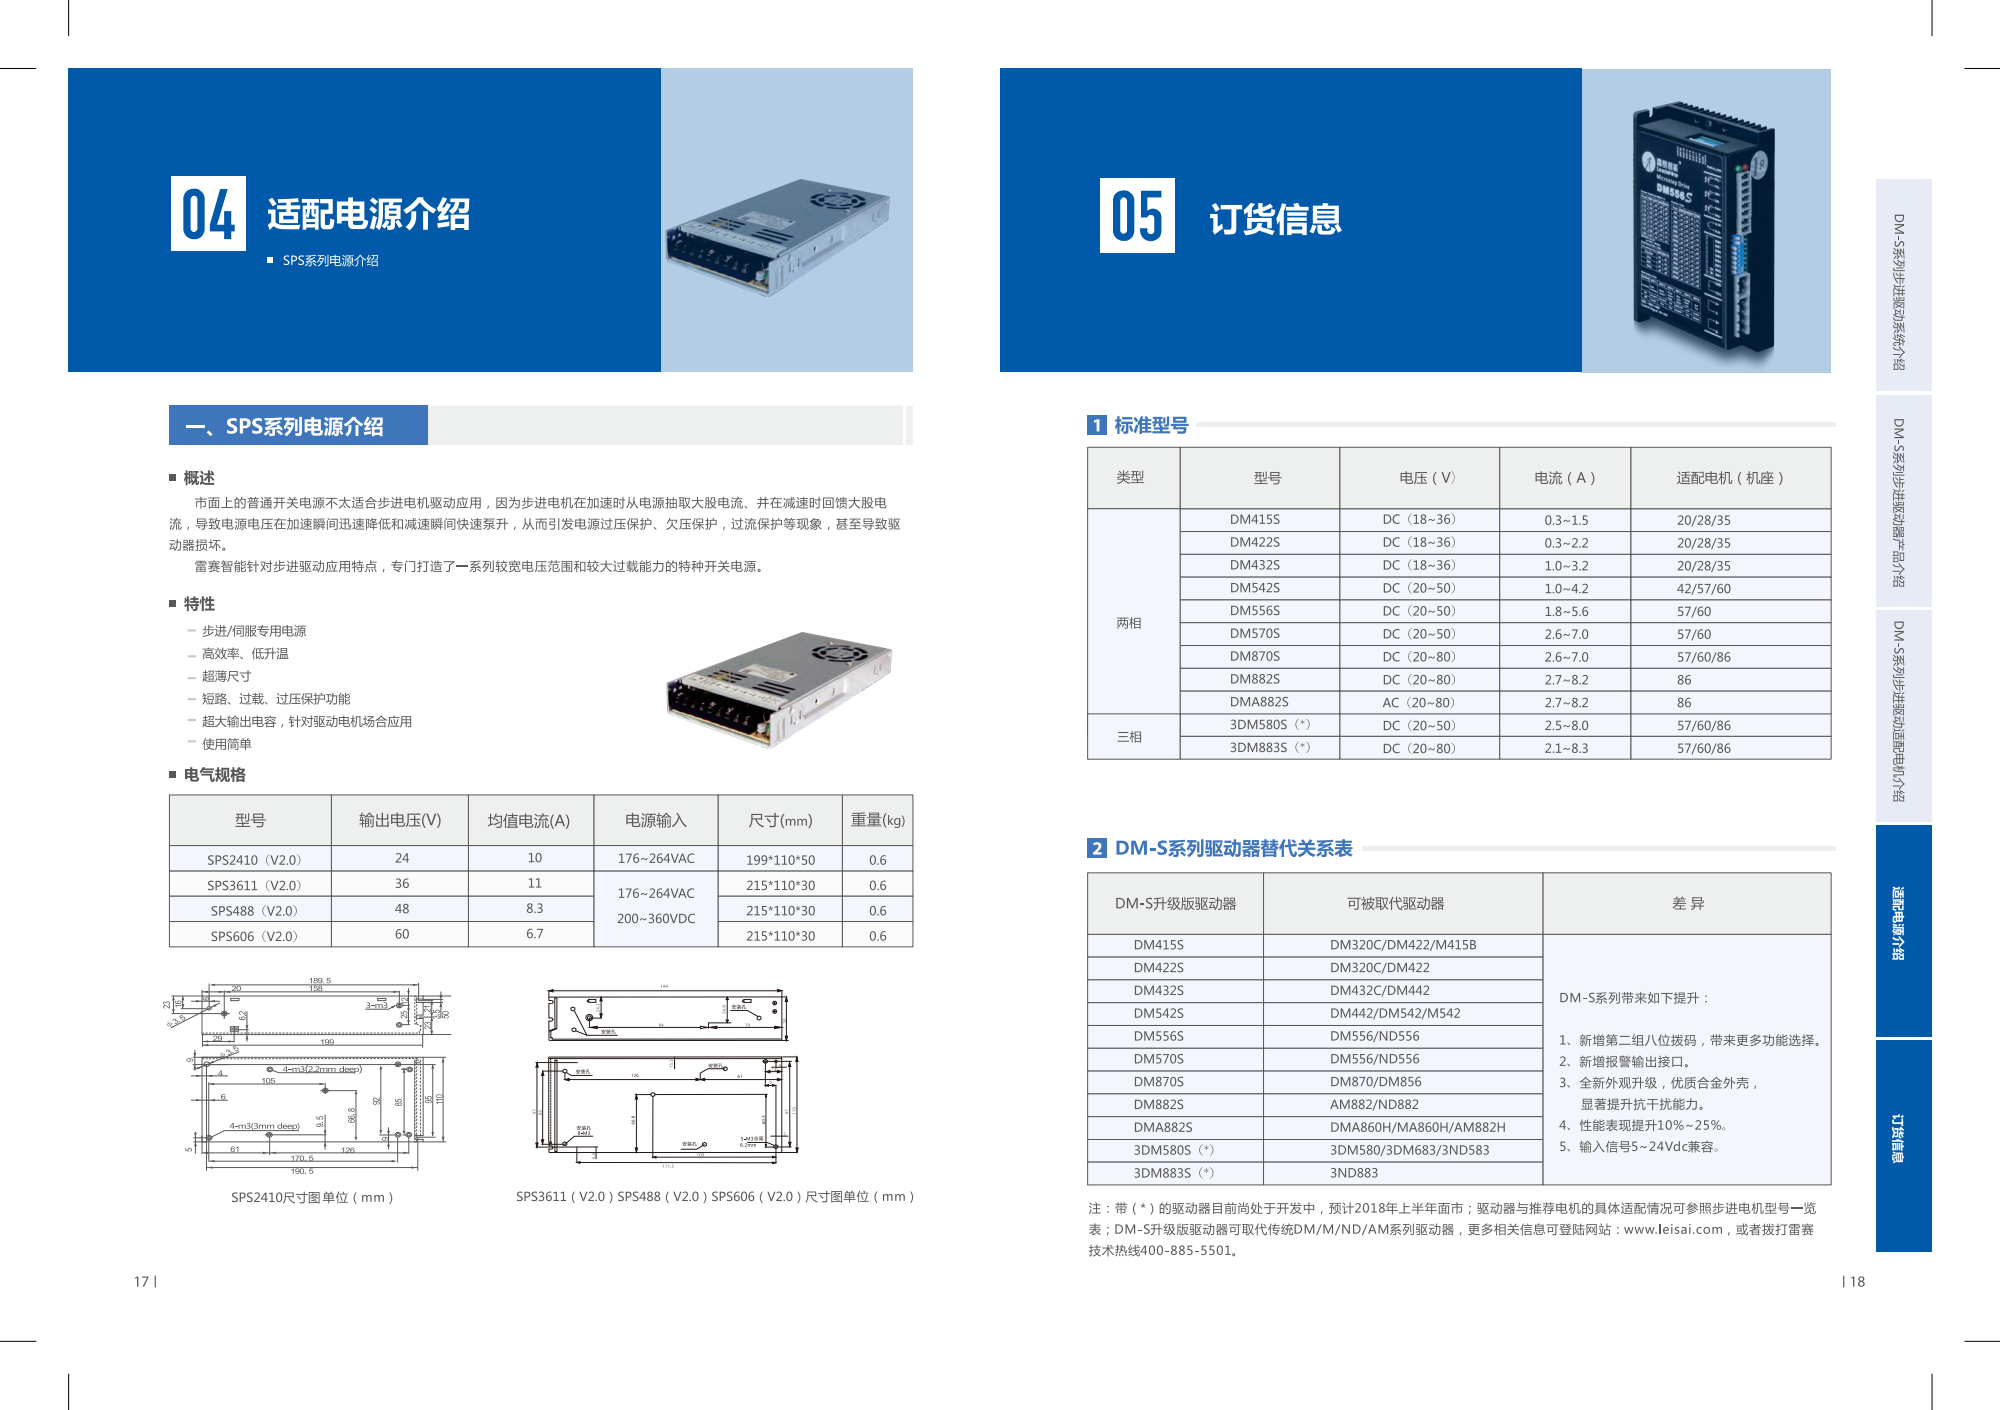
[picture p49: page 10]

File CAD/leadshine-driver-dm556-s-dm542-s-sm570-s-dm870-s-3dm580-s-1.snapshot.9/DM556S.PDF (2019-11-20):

Инв. № подл.; № докум.; Подп.; Дата; Формат А3

Подп. и дата Взам. инв. № Инв. № дубл. Подп. и дата

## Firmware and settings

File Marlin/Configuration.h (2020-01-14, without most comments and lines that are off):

#define CONFIGURATION_H
#define CONFIGURATION_H_VERSION 010109
#define STRING_CONFIG_H_AUTHOR "(none, default config)" // Who made the changes.
#define SHOW_BOOTSCREEN
#define STRING_SPLASH_LINE1 SHORT_BUILD_VERSION // will be shown during bootup in line 1
#define STRING_SPLASH_LINE2 "Daniel"            // will be shown during bootup in line 2
#define SERIAL_PORT 0
#define BAUDRATE 115200
#define MOTHERBOARD BOARD_RAMPS_14_EFB
#define CUSTOM_MACHINE_NAME "Daniel"
#define EXTRUDERS 1
#define DEFAULT_NOMINAL_FILAMENT_DIA 3.0
#define POWER_SUPPLY 0
#define TEMP_SENSOR_0       13
#define TEMP_SENSOR_1       0
#define TEMP_SENSOR_2       0
#define TEMP_SENSOR_3       0
#define TEMP_SENSOR_4       0
#define TEMP_SENSOR_BED     0
#define TEMP_SENSOR_CHAMBER 0
#define DUMMY_THERMISTOR_998_VALUE 25
#define DUMMY_THERMISTOR_999_VALUE 100
#define MAX_REDUNDANT_TEMP_SENSOR_DIFF 10
#define TEMP_RESIDENCY_TIME 10 // (seconds)
#define TEMP_HYSTERESIS     3  // (degC) range of +/- temperatures considered "close" to the target one
#define TEMP_WINDOW         1  // (degC) Window around target to start the residency timer x degC early.
#define TEMP_BED_RESIDENCY_TIME 10 // (seconds)
#define TEMP_BED_HYSTERESIS     3  // (degC) range of +/- temperatures considered "close" to the target one
#define TEMP_BED_WINDOW         1  // (degC) Window around target to start the residency timer x degC early.
#define HEATER_0_MINTEMP 5
#define HEATER_1_MINTEMP 5
#define HEATER_2_MINTEMP 5
#define HEATER_3_MINTEMP 5
#define HEATER_4_MINTEMP 5
#define BED_MINTEMP      5
#define HEATER_0_MAXTEMP 275
#define HEATER_1_MAXTEMP 275
#define HEATER_2_MAXTEMP 275
#define HEATER_3_MAXTEMP 275
#define HEATER_4_MAXTEMP 275
#define BED_MAXTEMP      150
#define PIDTEMP
#define BANG_MAX 255 // Limits current to nozzle while in bang-bang mode; 255=full current
#define PID_MAX BANG_MAX// Limits current to nozzle while PID is active (see
#define PID_K1 0.95 // Smoothing factor within any PID loop
#define PID_FUNCTIONAL_RANGE 10  // If the temperature difference between the target temperature and the actual temperature
#define DEFAULT_Kp 22.2
#define DEFAULT_Ki 1.08
#define DEFAULT_Kd 114
#define MAX_BED_POWER 255 // limits duty cycle to bed; 255=full current
#define PREVENT_COLD_EXTRUSION
#define EXTRUDE_MINTEMP 170
#define PREVENT_LENGTHY_EXTRUDE
#define EXTRUDE_MAXLENGTH 200
#define THERMAL_PROTECTION_HOTENDS // Enable thermal protection for all
#define THERMAL_PROTECTION_BED     // Enable thermal protection for the heated bed
#define USE_XMIN_PLUG
#define USE_YMIN_PLUG
#define USE_ZMIN_PLUG
#define USE_Joint1MIN_PLUG
#define USE_Joint2MIN_PLUG
#define USE_Joint3MIN_PLUG
#define USE_Joint4MIN_PLUG
#define USE_Joint5MIN_PLUG
#define USE_Joint1MAX_PLUG
#define USE_Joint2MAX_PLUG
#define USE_Joint3MAX_PLUG
#define USE_Joint4MAX_PLUG
#define USE_Joint5MAX_PLUG
#define ENDSTOPPULLUPS
#define X_MIN_ENDSTOP_INVERTING       false // set to true to invert the logic of the endstop.
#define Y_MIN_ENDSTOP_INVERTING       false // set to true to invert the logic of the endstop.
#define Z_MIN_ENDSTOP_INVERTING       false // set to true to invert the logic of the endstop.
#define X_MAX_ENDSTOP_INVERTING       false // set to true to invert the logic of the endstop.
#define Y_MAX_ENDSTOP_INVERTING       false // set to true to invert the logic of the endstop.
#define Z_MAX_ENDSTOP_INVERTING       false // set to true to invert the logic of the endstop.
#define Z_MIN_PROBE_ENDSTOP_INVERTING true  // set to true to invert the logic of the probe.
#define Joint1_MIN_ENDSTOP_INVERTING true
#define Joint2_MIN_ENDSTOP_INVERTING true
#define Joint3_MIN_ENDSTOP_INVERTING true
#define Joint4_MIN_ENDSTOP_INVERTING true
#define Joint5_MIN_ENDSTOP_INVERTING true
#define Joint1_MAX_ENDSTOP_INVERTING false
#define Joint2_MAX_ENDSTOP_INVERTING false
#define Joint3_MAX_ENDSTOP_INVERTING false
#define Joint4_MAX_ENDSTOP_INVERTING false
#define Joint5_MAX_ENDSTOP_INVERTING false
#define X_DRIVER_TYPE  TMC2100
#define Y_DRIVER_TYPE  TMC2100
#define DEFAULT_AXIS_STEPS_PER_UNIT {100.23, 99.86, 7999.52, 418.5}
#define DEFAULT_JOINT_STEPS_PER_UNIT {120, 60, 60, 60, 40}
#define DEFAULT_MAX_FEEDRATE {300, 300, 3, 25}
#define DEFAULT_MAX_FEEDRATE_JOINT {1.5, 50, 200, 200, 70}
#define DEFAULT_MAX_ACCELERATION {100, 100, 30, 10000}
#define DEFAULT_MAX_ACCELERATION_joint {13, 50, 15, 50, 50}
#define DEFAULT_ACCELERATION         25           // X, Y, Z and E acceleration for printing moves
#define DEFAULT_RETRACT_ACCELERATION 3000         // E acceleration for retracts
#define DEFAULT_TRAVEL_ACCELERATION  25           // X, Y, Z acceleration for travel (non printing) moves
#define DEFAULT_XJERK 0.01
#define DEFAULT_YJERK 0.01
#define DEFAULT_ZJERK 0.01
#define DEFAULT_JJERK 20
#define DEFAULT_AJERK 20
#define DEFAULT_BJERK 20
#define DEFAULT_CJERK 20
#define DEFAULT_DJERK 20
#define DEFAULT_EJERK 5.0
#define Z_MIN_PROBE_ENDSTOP
#define Z_PROBE_SERVO_NR 0 // Defaults to SERVO 0 connector.
#define Z_SERVO_ANGLES {90, 0} // Z Servo Deploy and Stow angles
#define X_PROBE_OFFSET_FROM_EXTRUDER 27 // X offset: -left  +right  [of the nozzle]
#define Y_PROBE_OFFSET_FROM_EXTRUDER 7 // Y offset: -front +behind [the nozzle]
#define Z_PROBE_OFFSET_FROM_EXTRUDER 12.7  //26.55  // Z offset: -below +above  [the nozzle]
#define MIN_PROBE_EDGE 10
#define XY_PROBE_SPEED 50*60//8000
#define Z_PROBE_SPEED_FAST HOMING_FEEDRATE_Z
#define Z_PROBE_SPEED_SLOW (Z_PROBE_SPEED_FAST / 2)
#define MULTIPLE_PROBING 2
#define Z_CLEARANCE_DEPLOY_PROBE   25 // Z Clearance for Deploy/Stow
#define Z_CLEARANCE_BETWEEN_PROBES 5  // Z Clearance between probe points
#define Z_CLEARANCE_MULTI_PROBE    5  // Z Clearance between multiple probes
#define Z_PROBE_LOW_POINT -2 // Farthest distance below the trigger-point to go before stopping
#define Z_PROBE_OFFSET_RANGE_MIN -20
#define Z_PROBE_OFFSET_RANGE_MAX 20
#define X_ENABLE_ON 0
#define Y_ENABLE_ON 0
#define Z_ENABLE_ON 0
#define E_ENABLE_ON 0 // For all extruders
#define Joint1_ENABLE_ON 0
#define Joint2_ENABLE_ON 0
#define Joint3_ENABLE_ON 0
#define Joint4_ENABLE_ON 0
#define Joint5_ENABLE_ON 0
#define DISABLE_X false
#define DISABLE_Y false
#define DISABLE_Z false
#define DISABLE_Joint1 false
#define DISABLE_Joint2 false
#define DISABLE_Joint3 false
#define DISABLE_Joint4 false
#define DISABLE_Joint5 false
#define DISABLE_E                 false // For all extruders
#define DISABLE_INACTIVE_EXTRUDER true  // Keep only the active extruder enabled.
#define INVERT_X_DIR false
#define INVERT_Y_DIR true
#define INVERT_Z_DIR false
#define INVERT_Joint1_DIR false
#define INVERT_Joint2_DIR false
#define INVERT_Joint3_DIR false
#define INVERT_Joint4_DIR false
#define INVERT_Joint5_DIR false
#define INVERT_E0_DIR false
#define INVERT_E1_DIR false
#define INVERT_E2_DIR false
#define INVERT_E3_DIR false
#define INVERT_E4_DIR false
#define X_HOME_DIR -1
#define Y_HOME_DIR -1
#define Z_HOME_DIR -1
#define Joint1_HOME_DIR -1
#define Joint2_HOME_DIR -1
#define Joint3_HOME_DIR -1
#define Joint4_HOME_DIR -1
#define Joint5_HOME_DIR -1
#define X_BED_SIZE 200
#define Y_BED_SIZE 200
#define X_MIN_POS 0
#define Y_MIN_POS 0
#define Z_MIN_POS 0
#define X_MAX_POS X_BED_SIZE
#define Y_MAX_POS Y_BED_SIZE
#define Z_MAX_POS 200
#define J_MIN_POS_step -12400
#define A_MIN_POS_step -41080
#define B_MIN_POS_step -99280
#define C_MIN_POS_step -37990
#define D_MIN_POS_step -18560
#define J_MAX_POS_step 12400
#define A_MAX_POS_step 42000
#define B_MAX_POS_step 100000
#define C_MAX_POS_step 111810
#define D_MAX_POS_step 20500
#define Joint1_MIN_POS -12400
#define Joint2_MIN_POS -41080
#define Joint3_MIN_POS -99280
#define Joint4_MIN_POS -37990
#define Joint5_MIN_POS -18560
#define Joint1_MAX_POS 12400
#define Joint2_MAX_POS 42000
#define Joint3_MAX_POS 110000
#define Joint4_MAX_POS 118110
#define Joint5_MAX_POS 20500
#define MIN_SOFTWARE_ENDSTOPS
#define MIN_SOFTWARE_ENDSTOP_X
#define MIN_SOFTWARE_ENDSTOP_Y
#define MIN_SOFTWARE_ENDSTOP_Z
#define MIN_SOFTWARE_ENDSTOP_J
#define MIN_SOFTWARE_ENDSTOP_A
#define MIN_SOFTWARE_ENDSTOP_B
#define MIN_SOFTWARE_ENDSTOP_C
#define MIN_SOFTWARE_ENDSTOP_D
#define MAX_SOFTWARE_ENDSTOPS
#define MAX_SOFTWARE_ENDSTOP_X
#define MAX_SOFTWARE_ENDSTOP_Y
#define MAX_SOFTWARE_ENDSTOP_Z
#define MAX_SOFTWARE_ENDSTOP_J
#define MAX_SOFTWARE_ENDSTOP_A
#define MAX_SOFTWARE_ENDSTOP_B
#define MAX_SOFTWARE_ENDSTOP_C
#define MAX_SOFTWARE_ENDSTOP_D
#define AUTO_BED_LEVELING_LINEAR
#define RESTORE_LEVELING_AFTER_G28
#define DEBUG_LEVELING_FEATURE
#define GRID_MAX_POINTS_X 5
#define GRID_MAX_POINTS_Y GRID_MAX_POINTS_X
#define HOMING_FEEDRATE_XY    (50 * 60)
#define HOMING_FEEDRATE_Z     (50 * 60)//(4 * 60)
#define HOMING_FEEDRATE_Joint (50 * 60)
#define EEPROM_SETTINGS // Enable for M500 and M501 commands
#define DISABLE_M503    // Saves ~2700 bytes of PROGMEM. Disable for release!
#define EEPROM_CHITCHAT // Give feedback on EEPROM commands. Disable to save
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

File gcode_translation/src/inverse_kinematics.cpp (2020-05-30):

#include <moveit/planning_scene_interface/planning_scene_interface.h>
#include <moveit/planning_scene/planning_scene.h>
#include <moveit/move_group_interface/move_group_interface.h>
#include <moveit/kinematic_constraints/utils.h>
#include <moveit/robot_model_loader/robot_model_loader.h>
#include <moveit_msgs/AttachedCollisionObject.h>
#include <moveit_msgs/CollisionObject.h>
#include <trac_ik/trac_ik.hpp>
#include <ros/ros.h>
#include <tf/tf.h>
#include <math.h>
#include <omp.h>
#include <std_msgs/Float64MultiArray.h>
#include <include/Mesh/circle_new.h>
#include <include/Joint_division/joint_division.hpp>

// Let gocde look more clearly 
int decimal_point(double &A){
  std::string change = std::to_string(A);
  bool point = false;
  for(int i = 0;i<change.size();i++){
    if(change[i] == '.') point = true;
    if(point == true){
      if(change[i+3] == '0'){
        if(change[i+2] == '0'){
          if(change[i+1] == '0') return 0;
          return 1;
        }
        return 2;
      }
      return 3;
    }
  }
}

// Use tf to translate 
tf::Quaternion euler_to_quaternion(double yaw,double pitch,double roll){
  tf::Quaternion q;
  q.setRPY(yaw,pitch,roll);
  return q;
}

// Chrck the basic setting
bool check_trac_ik_valid(TRAC_IK::TRAC_IK &tracik_solver,KDL::Chain &chain, KDL::JntArray &ll, KDL::JntArray &ul){
  bool valid = tracik_solver.getKDLChain(chain);
  //ROS_INFO_NAMED("moveo", "TRAC-IK setup");
  if (!valid){
    ROS_ERROR("There was no valid KDL chain found");
    return false;
  }
  valid = tracik_solver.getKDLLimits(ll, ul);
  if (!valid){
    ROS_ERROR("There were no valid KDL joint limits found");
    return false;
  }
  return true;
}

// Translate the data from angle to steps
void motor_steps_convert(Eigen::VectorXd &data, bool &judge, KDL::Chain &chain, std::vector<double> &joint_division){
  if(!judge){
    for(int i = 0; i < chain.getNrOfJoints(); i++){
      data(i) = data(i)/(M_PI)*180*joint_division[i]/360;
    }
  }
  else{
    for(int i = 0; i < chain.getNrOfJoints(); i++){
      data(i) = data(i)*(M_PI)/180/joint_division[i]*360;
    }
  }
}

// Write output joint values(step) in the gcode
void write_file_joint_value(std::ofstream &output_file, KDL::JntArray &result, KDL::Chain &chain, std::vector<double> &joint_division){
  bool judge = false;
  motor_steps_convert(result.data, judge, chain, joint_division);
  for(int i = 0;i < chain.getNrOfJoints(); i++){
    static const char joint_code[6] = {'J', 'A', 'B', 'C', 'D'};
    output_file << " " << joint_code[i] << int(result.data(i));
  }
}

// If the line is not G1 or G0, that we just write it's original data
void write_file_origin_line(std::ofstream &output_file, std::string &line){
  for(int j = 2;j < line.length(); j++){
    output_file << line[j];
  }
}

// If joint4 has change 180 degrees, we have to creat a new line that the point is the same in gcode.
// That means, we have to rotate the joint4 but, it must stay at the same position
void write_file_new_point(std::ofstream &output_file, KDL::Vector &output_end_effector_target_vol, double &X_offset, double &Y_offset){
  double decimal_x = (output_end_effector_target_vol.data[0]-X_offset)*1e3;
  double decimal_y = (output_end_effector_target_vol.data[1]-Y_offset)*1e3;
  output_file << std::fixed << std::setprecision(decimal_point(decimal_x)) << " X" << decimal_x << std::defaultfloat;
  output_file << std::fixed << std::setprecision(decimal_point(decimal_y)) << " Y" << decimal_y << std::defaultfloat;
}

// Write the position that we give the joint values
void customize_joint(std::ofstream &output_file, KDL::Frame &end_effector_pose){
  double decimal_x = end_effector_pose.p.x()*1000;
  double decimal_y = end_effector_pose.p.y()*1000;
  double decimal_z = end_effector_pose.p.z()*1000;
  output_file << std::fixed << std::setprecision(decimal_point(decimal_x)) << " X" << decimal_x << std::defaultfloat;
  output_file << std::fixed << std::setprecision(decimal_point(decimal_y)) << " Y" << decimal_y << std::defaultfloat;
  output_file << std::fixed << std::setprecision(decimal_point(decimal_z)) << " Z" << decimal_z << std::defaultfloat << " ";
}

// Write customize_joint to gcode
void write_customize_joint(std::ofstream &output_file, std::string &line, KDL::Chain &chain, std::vector<double> &joint_division){
  KDL::ChainFkSolverPos_recursive fk_solver(chain);
  KDL::JntArray Joint(chain.getNrOfJoints());
  KDL::Frame end_effector_pose;
  output_file << line[0] << line[1];
  if(line.find('F') != std::string::npos && stoi(line.substr(line.find('F')+1)) != 0) output_file << " F" << stoi(line.substr(line.find('F')+1));
  static const char joint_code[6] = {'J', 'A', 'B', 'C', 'D'};
  for(int i = 0;i < chain.getNrOfJoints();i++){
    Joint(i) = stod(line.substr(line.find(joint_code[i])+1));
    output_file << " " << joint_code[i] << int(Joint(i));
  }
  bool judge = true;
  motor_steps_convert(Joint.data, judge, chain, joint_division);
  fk_solver.JntToCart(Joint, end_effector_pose);
  customize_joint(output_file, end_effector_pose);
  if(line.find(';') != std::string::npos) for(int i = line.find(';');i < line.length();i++) output_file << line[i];
  output_file << std::endl;
}

// If the translation has some error, that we will write it position, joint value and quaternion
void show_error_point_and_joint(KDL::Vector &end_effector_target_vol, KDL::Chain &chain, KDL::JntArray &result, tf::Quaternion &q, int &p_n, std::vector<double> &joint_division){
  ROS_ERROR_STREAM("===============Position===============");
  ROS_ERROR_STREAM("X : " << end_effector_target_vol.data[0]);
  ROS_ERROR_STREAM("Y : " << end_effector_target_vol.data[1]);
  ROS_ERROR_STREAM("Z : " << end_effector_target_vol.data[2]);
  ROS_ERROR_STREAM("=============Joint Values=============");
  //bool judge = false;
  //motor_steps_convert(result.data, judge, chain, joint_division);
  for(int i = 0;i < chain.getNrOfJoints(); i++){
    static const char joint_code[6] = {'J', 'A', 'B', 'C', 'D'};
    ROS_ERROR_STREAM(joint_code[i] << " : " << result.data(i));
  }
  ROS_ERROR_STREAM("==============Quaternion==============");
  ROS_ERROR_STREAM(q[0] << " , " << q[1] << " , " << q[2] << " , " << q[3]);
  ROS_ERROR_STREAM("==================PN==================");
  ROS_ERROR_STREAM(p_n);
}

// Send data to the progressbar
void publisher_to_progressbar(ros::Publisher &translation_pub, int &save_all_line, int &save_all_read_line_count, double &need_times){
  std_msgs::Float64MultiArray push_data;
  push_data.data.resize(3);
  push_data.data[0] = save_all_line;               // gcode all lines
  push_data.data[1] = save_all_read_line_count;    // now we write how many lines
  push_data.data[2] = need_times;                  // writing 1000 lines needs times (average)
  translation_pub.publish(push_data);              // push to progressbar.cpp 
}

// If split finish, that we can start this code
bool start_judge = false;
void start(const std_msgs::Float64MultiArray& receive){
  start_judge = true;
}

ros::WallTime start_, end_;
ros::WallTime start_first_, end_first_;
int main(int argc, char **argv){
  ros::init(argc, argv, "inverse_kinematicks");
  ros::NodeHandle node_handle("~");
  ros::AsyncSpinner spinner(1);
  spinner.start();

  ros::Publisher translation_pub = node_handle.advertise<std_msgs::Float64MultiArray>("progress", 1000); // push time needed to progressbar
  ros::Publisher start_pub = node_handle.advertise<std_msgs::Float64MultiArray>("progress_start", 1000); // push start to progressbar
  ros::Publisher respond_split_pub = node_handle.advertise<std_msgs::Float64MultiArray>("respond", 1000);
  ros::Subscriber split_sub = node_handle.subscribe("/gcode_translation/start", 100000, start); // get start from gcode_point_split

  // Wait split finish
  while(!start_judge){
    if(ros::ok()) ros::spinOnce();
    else return -1;
  }
  start_first_ = ros::WallTime::now();

  std_msgs::Float64MultiArray push;
  push.data.resize(1);
  push.data[0] = 1;
  respond_split_pub.publish(push);
  start_pub.publish(push);

  //----------------------------
  //Setup
  //----------------------------
  std::string chain_start, chain_end, urdf_param, urdf_param_turn;
  double timeout,timeout_second,eps;
  double X_offset, Y_offset, Z_offset;
  int num_threads;
  node_handle.param("chain_start", chain_start, std::string(""));
  node_handle.param("chain_end", chain_end, std::string(""));
  if (chain_start == "" || chain_end == ""){
    ROS_FATAL("Missing chain info in launch file");
    exit(-1);
  }
  node_handle.param("timeout", timeout, 0.05);
  node_handle.param("timeout_second", timeout_second, 0.1);
  node_handle.param("urdf_param", urdf_param, std::string("/robot_description"));
  node_handle.param("urdf_param_turn", urdf_param_turn, std::string("/robot_description2"));
  node_handle.param("eps", eps, 1e-5);
  node_handle.param("num_threads", num_threads, omp_get_num_procs()*2);
  node_handle.param("X_offset", X_offset, 0.0);
  node_handle.param("Y_offset", Y_offset, 0.0);
  node_handle.param("Z_offset", Z_offset, 0.0);

  KDL::Chain chain;
  KDL::JntArray ll, ul; //lower joint limits, upper joint limits

  //----------------------------
  //TRAC_IK setup
  //----------------------------
  // Joint4 doesn't need to turn
  TRAC_IK::TRAC_IK** tracik_solver = new TRAC_IK::TRAC_IK*[num_threads];
  for(int i = 0; i < num_threads; i++){
    tracik_solver[i] = new TRAC_IK::TRAC_IK(chain_start, chain_end, urdf_param, timeout, eps, TRAC_IK::Speed);
    if(!check_trac_ik_valid(*tracik_solver[i], chain, ll, ul)) return -1;
  }
  TRAC_IK::TRAC_IK tracik_solver_onecore(chain_start, chain_end, urdf_param, timeout_second, eps, TRAC_IK::Speed);
  if(!check_trac_ik_valid(tracik_solver_onecore, chain, ll, ul)) return -1;

  // Joint4 needs to turn
  TRAC_IK::TRAC_IK** tracik_solver_turn = new TRAC_IK::TRAC_IK*[num_threads];
  for(int i = 0; i < num_threads; i++){
    tracik_solver_turn[i] = new TRAC_IK::TRAC_IK(chain_start, chain_end, urdf_param_turn, timeout, eps, TRAC_IK::Speed);
    if(!check_trac_ik_valid(*tracik_solver_turn[i], chain, ll, ul)) return -1;
  }
  TRAC_IK::TRAC_IK tracik_solver_onecore_turn(chain_start, chain_end, urdf_param_turn, timeout_second, eps, TRAC_IK::Speed);
  if(!check_trac_ik_valid(tracik_solver_onecore_turn, chain, ll, ul)) return -1;

  TRAC_IK::TRAC_IK tracik_solver_p_n(chain_start, chain_end, urdf_param_turn, timeout_second, eps, TRAC_IK::Speed);
  if(!check_trac_ik_valid(tracik_solver_p_n, chain, ll, ul)) return -1;

  assert(chain.getNrOfJoints() == ll.data.size());
  assert(chain.getNrOfJoints() == ul.data.size());

  // Create Nominal chain configuration midway between all joint limits
  KDL::JntArray nominal(chain.getNrOfJoints());
  for (uint j = 0; j < nominal.data.size(); j++){
    nominal(j) = (ll(j) + ul(j)) / 2.0;
  }

  //----------------------------
  // Setting robot collision
  //----------------------------
  robot_model_loader::RobotModelLoader robot_model_loader("robot_description");
  robot_model::RobotModelPtr kinematic_model = robot_model_loader.getModel();
  planning_scene::PlanningScene planning_scene(kinematic_model);
  collision_detection::CollisionRequest collision_request;
  collision_detection::CollisionResult collision_result;
  planning_scene.checkSelfCollision(collision_request, collision_result);
  ROS_INFO_STREAM("Test: Current state is " << (collision_result.collision ? "in" : "not in") << " self collision");
  robot_state::RobotState& current_state = planning_scene.getCurrentStateNonConst();
  collision_request.group_name = "arm";

  // Read joint division
  std::vector<double> joint_division;
  std::string joint_division_name;
  node_handle.param("joint_division", joint_division_name, std::string("/joint_division"));
  joint_division = read_joint_division(joint_division_name, chain.getNrOfJoints());

  std::string line;                     // getline used
  KDL::Vector end_effector_target_vol;  // Read gcode xyz
  // Read all lines of gcode
  std::string gcode_in;
  node_handle.param("gcode_in", gcode_in, std::string("/gcode_in"));
  std::ifstream input_file(gcode_in);
  if(!input_file.is_open()) ROS_ERROR_STREAM("Can't open " << gcode_in);
  int save_all_line = 0;
  bool check_first_point = false;
  while(input_file){
    std::getline(input_file, line);
    if(!check_first_point){
      // Find the first point position
      if((!line.compare(0,2,"G0") || !line.compare(0,2,"G1")) && line.find('X') != std::string::npos && line.find('Y') != std::string::npos && line.find('Z') != std::string::npos){
        check_first_point = true;
        end_effector_target_vol.data[0] = stod(line.substr(line.find('X')+1));
        end_effector_target_vol.data[1] = stod(line.substr(line.find('Y')+1));
        end_effector_target_vol.data[2] = stod(line.substr(line.find('Z')+1))+25;
        save_all_line++;
      }
    }
    save_all_line++;
  }
  input_file.close();
  ROS_INFO_STREAM("Read all lines success");

  // Read gcode
  input_file.open(gcode_in);

  // Write gcode
  std::string gcode_out;
  node_handle.param("gcode_out", gcode_out, std::string("/gcode_out"));
  std::ofstream output_file(gcode_out);
  if(!output_file.is_open()) ROS_ERROR_STREAM("Can't open " << gcode_out);

  std::vector<std::string> save;  // Save original gcode lines
  save.reserve(1000);
  KDL::Vector previous_end_effector_target_vol;
  int previous_save_p_or_n;
  float previous_angle;

  KDL::Vector target_bounds_rot(0, 0, M_PI*2);
  KDL::Vector target_bounds_vel(0,0,0);
  const KDL::Twist target_bounds(target_bounds_vel, target_bounds_rot);

  bool first_point = true;
  int read_line_count = 0;
  int save_count = 0;
  int second_execution = 0;
  int save_all_read_line_count = 0;
  double z_init = 0;
  double save_all_need_times = 0;

  Load_Mesh(35.25);
  Calc_abcd();

  while(input_file){
    if(ros::ok()){
      std::getline(input_file, line);
      // Creat one position that is 25mm taller than first position
      if(!line.compare(0,4,"M400") && check_first_point){
        check_first_point = false;
        std::ostringstream store;
        store << "G1 F2000 X" << end_effector_target_vol.data[0] << " Y" << end_effector_target_vol.data[1] << " Z" << end_effector_target_vol.data[2];
        save.emplace_back(std::move(store.str()));
        store.clear();
        read_line_count++;
      }
      save.emplace_back(std::move(line));
      read_line_count++;
      if(read_line_count % 1000 == 0 || !input_file){ // Read 1000 lines or end of file
        start_ = ros::WallTime::now();
        std::vector<KDL::Vector> find_end_effector_target_vol;  // Filtrate not G1 or G0
        find_end_effector_target_vol.reserve(1000);
        std::vector<float> find_angle;                          // Each point angle
        find_angle.reserve(1000);
        std::vector<int> save_place;                            // Find position of G1 and G0 
        save_place.reserve(1000);
        std::vector<int> save_p_or_n;                           // Save joint4 needs to turn or not 
        save_p_or_n.reserve(1000);
        for(int i = 0;i < read_line_count ;i++){
          line = save[i];
          if((!line.compare(0,2,"G0") || !line.compare(0,2,"G1")) && (line.find('J') == std::string::npos)){
            if(line.find('X') != std::string::npos) end_effector_target_vol.data[0] = (stod(line.substr(line.find('X')+1))*1e-3)+X_offset;
            if(line.find('Y') != std::string::npos) end_effector_target_vol.data[1] = (stod(line.substr(line.find('Y')+1))*1e-3)+Y_offset;
            if(line.find('Z') != std::string::npos) z_init = (stod(line.substr(line.find('Z')+1))*1e-3)+Z_offset;
            
            double z_pos = calc_z_rectangle(end_effector_target_vol.data[0], end_effector_target_vol.data[1], true); // Unit: m -> mm
            if (z_pos == (std::numeric_limits<double>::max)()){
              ROS_INFO_STREAM("Out of rectangle area");
              return -1;
            }
            // 9.18 nozzle high
            end_effector_target_vol.data[2] = z_init + z_pos;
            find_end_effector_target_vol.emplace_back(std::move(end_effector_target_vol));
            save_place.emplace_back(std::move(i));
            // Calculate position angle
            float position_angel = asin(end_effector_target_vol.data[0] / sqrt(pow(end_effector_target_vol.data[0],2)+pow(end_effector_target_vol.data[1],2)));
            
            if(end_effector_target_vol.data[1] > 0) position_angel = position_angel * (-1);
            else position_angel = position_angel + M_PI;
            if(sqrt(pow(end_effector_target_vol.data[0]*100,2)+pow(end_effector_target_vol.data[1]*100,2)) <= 35){
              position_angel = position_angel + M_PI;
              save_p_or_n.emplace_back(std::move(0));
            }
            else save_p_or_n.emplace_back(std::move(1));
            find_angle.emplace_back(std::move(position_angel));
          }
        }
        std::vector<KDL::JntArray> save_result(1000);
        std::vector<int> save_use_onecore(1000);
        // Use paralleled TRAC-IK to calculate
        omp_set_num_threads(num_threads);
        #pragma omp parallel for
        for(int j = 0;j < save_place.size();j++){
          int rc = -1;
          int thread_num = omp_get_thread_num();
          KDL::JntArray result;
          tf::Quaternion q = euler_to_quaternion(0.0,0.0,find_angle[j]);
          KDL::Rotation end_effector_target_rot = KDL::Rotation::Quaternion(q[0],q[1],q[2],q[3]);
          KDL::Frame end_effector_pose(end_effector_target_rot, find_end_effector_target_vol[j]);

          if(save_p_or_n[j] == 0) rc = tracik_solver_turn[thread_num]->CartToJnt(nominal, end_effector_pose, result, target_bounds); // Need turn
          else rc = tracik_solver[thread_num]->CartToJnt(nominal, end_effector_pose, result, target_bounds);

          if(rc < 0) save_use_onecore[j] = 1; // Parallel TRAC-IK can't calculate
          else{
            save_use_onecore[j] = 0;
            save_result[j] = result;
          }
        }
        if(save_use_onecore.size() > 0){
          std::vector<int> use_onecore;
          use_onecore.reserve(1000);
          // Calculate which line need to use one core to calculate 
          for(auto k = save_use_onecore.begin();k < save_use_onecore.end();k++){
            if(*k == 1) use_onecore.emplace_back(std::move(*k));
          }
          save_use_onecore.clear();
          save_use_onecore.shrink_to_fit();
          // Use one core to calculate
          for(auto l = use_onecore.begin();l < use_onecore.end();l++){
            int rc = -1;
            second_execution++;
            KDL::JntArray result;
            tf::Quaternion q = euler_to_quaternion(0.0,0.0,find_angle[*l]);
            KDL::Rotation end_effector_target_rot = KDL::Rotation::Quaternion(q[0],q[1],q[2],q[3]);
            KDL::Frame end_effector_pose(end_effector_target_rot, find_end_effector_target_vol[*l]);

            if(save_p_or_n[*l] == 0) rc = tracik_solver_onecore_turn.CartToJnt(nominal, end_effector_pose, result, target_bounds);
            else rc = tracik_solver_onecore.CartToJnt(nominal, end_effector_pose, result, target_bounds);
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

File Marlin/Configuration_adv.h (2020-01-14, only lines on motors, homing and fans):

#define E0_AUTO_FAN_PIN -1
#define E1_AUTO_FAN_PIN -1
#define E2_AUTO_FAN_PIN -1
#define E3_AUTO_FAN_PIN -1
#define E4_AUTO_FAN_PIN -1
#define CHAMBER_AUTO_FAN_PIN -1
#define X_HOME_BUMP_MM 5
#define Y_HOME_BUMP_MM 5
#define Z_HOME_BUMP_MM 2
#define Joint1_HOME_BUMP_MM 620
#define Joint2_HOME_BUMP_MM 2230
#define Joint3_HOME_BUMP_MM 6085
#define Joint4_HOME_BUMP_MM 8640
#define Joint5_HOME_BUMP_MM 2045
#define HOMING_BUMP_DIVISOR {2, 2, 4} // Re-Bump Speed Divisor (Divides the Homing Feedrate)
#define HOMING_BUMP_DIVISOR_Joint {24, 9, 1.8, 1.8, 5}
#define MICROSTEP_MODES {16, 16, 16, 16, 16} // [1,2,4,8,16]
#define DIGIPOT_I2C_MOTOR_CURRENTS {1.0, 1.0, 1.0, 1.0, 1.0, 1.0, 1.0, 1.0} //  AZTEEG_X3_PRO

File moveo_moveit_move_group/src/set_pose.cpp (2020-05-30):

#include <moveit/move_group_interface/move_group_interface.h>
#include <moveit/planning_scene_interface/planning_scene_interface.h>
#include <moveit_msgs/DisplayRobotState.h>
#include <moveit_msgs/DisplayTrajectory.h>
#include <moveit_msgs/AttachedCollisionObject.h>
#include <moveit_msgs/CollisionObject.h>
#include <moveit_visual_tools/moveit_visual_tools.h>
#include <trac_ik/trac_ik.hpp>
#include <ros/ros.h>
#include <tf/tf.h>
#include <include/Joint_division/joint_division.hpp>

tf::Quaternion euler_to_quaternion(double yaw,double pitch,double roll);

void motor_steps_convert(Eigen::VectorXd &data, KDL::Chain &chain, std::vector<double> &joint_division){
  for(int i = 0; i < chain.getNrOfJoints(); i++){
    data(i) = data(i)/(M_PI)*180*joint_division[i]/360;
    ROS_INFO_STREAM("Joint" << (i+1) << " = " << int(data(i)));
  }
}

std::vector<double> solveJoint(KDL::Frame end_effector_pose){
  ros::NodeHandle node_handle("~");
  //init TRAC_IK
  std::string chain_start, chain_end, urdf_param;
  double timeout;
  node_handle.param("chain_start", chain_start, std::string(""));
  node_handle.param("chain_end", chain_end, std::string(""));
  if (chain_start == "" || chain_end == "")
  {
    ROS_FATAL("Missing chain info in launch file");
    exit(-1);
  }
  node_handle.param("timeout", timeout, 0.1);
  node_handle.param("urdf_param", urdf_param, std::string("/robot_description"));

  double eps = 1e-5;
  node_handle.param("eps", eps, 1e-5);
  ROS_INFO_STREAM("eps :" << eps);
  TRAC_IK::TRAC_IK tracik_solver(chain_start, chain_end, urdf_param, timeout, eps, TRAC_IK::Speed);

  KDL::Chain chain;
  KDL::JntArray ll, ul; //lower joint limits, upper joint limits

  bool valid = tracik_solver.getKDLChain(chain);
  ROS_INFO_NAMED("moveo", "TRAC-IK setup");
  if (!valid)
  {
    ROS_ERROR("There was no valid KDL chain found");
    exit(-1);
  }

  valid = tracik_solver.getKDLLimits(ll, ul);

  if (!valid)
  {
    ROS_ERROR("There were no valid KDL joint limits found");
    exit(-1);
  }

  assert(chain.getNrOfJoints() == ll.data.size());
  assert(chain.getNrOfJoints() == ul.data.size());
  ROS_INFO("Using %d joints", chain.getNrOfJoints());

  std::string joint_division_name;
  node_handle.param("joint_division", joint_division_name, std::string("/joint_division"));
  std::vector<double> joint_division = read_joint_division(joint_division_name, chain.getNrOfJoints());
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

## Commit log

2019-09-18 change urdf and moveo_moveit_config
    [base_link.STL, end_effector_link.STL, fake_controllers.yaml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]
2019-09-20 change urdf and moveit_config
    [end_effector_link.STL, moveo_link1.STL, moveo_link2.STL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]
2019-09-20 add nozzle to urdf and chage moveit_config
    [fake_controllers.yaml, moveo_urdf.urdf]
2019-09-20 create function solveJoint(KDL::Frame) to solve IK with TRAC-IK
2019-09-20 create function print_current_pose(geometry_msgs::PoseStamped)
2019-09-21 fix bug can't draw trajectoryLine on rviz
    [fake_controllers.yaml, moveo_link1.STL, moveo_link2.STL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]
2019-09-21 add rostopic chain_end_pose
2019-09-21 change target frame to nozzle
    [moveo_link1.STL, moveo_link2.STL, moveo_link3.STL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]
2019-09-24 update nozzle in urdf
    [fake_controllers.yaml, moveo_link1.STL, moveo_link2.STL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]
2019-09-27 chang ompl planner to LazyPRM
    [moveo_urdf.urdf]
2019-10-01 straight line
    [moveo_urdf.urdf]
2019-10-12 Add endstop
    [Configuration.h, Configuration_adv.h]
2019-10-14 No print detail
    [Configuration.h]
2019-10-14 Fix stepper
    [Configuration.h, Configuration_adv.h]
2019-10-14 set default thread num = core*2
2019-10-16 Fix G28
    [Configuration.h]
2019-10-17 Fix G29(No Joint)
    [Configuration.h]
2019-10-18 Fix G28(can go to zero)
    [Configuration_adv.h]
2019-10-21 Add M302 P1 in lcd Menu
    [Configuration.h]
2019-10-22 Fix lcd moving
    [Configuration_adv.h]
2019-10-23 Add Joint Slope Move
    [Configuration.h]
2019-10-24 Add Joint Curve Move
2019-11-01 Add Forward_Curve
    [Configuration.h, Configuration_adv.h]
2019-11-05 add Solidworks File
    [1M1.STL, 1M1B.SLDPRT, 1M2.STL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]
2019-11-06 Fix '\'
    [Configuration.h, Configuration_adv.h]
2019-11-06 finish 42stepper pcb layout
    [uStepper.PcbDoc, uStepper.PrjPcb, uStepper.SchDoc]
2019-11-07 add pcb place in 3M2C
    [3M2.SLDASM, 3M2C.SLDPRT]
2019-11-09 add limit switch in 3M2
    [3M2.SLDASM, 3M2C.SLDPRT, 3M2C.STL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]
2019-11-09 add 35 stepper pcb board
    [uStepper.PcbDoc, uStepper.PrjPcb, uStepper.SchDoc]
2019-11-12 Fix Memry High memory usage
    [Configuration.h, Configuration_adv.h]
2019-11-12 Fix backslash
    [Configuration.h, Configuration_adv.h]
2019-11-12 add 35uStepper PCB CAD file
    [+5.sldasm, 3M2.SLDASM, 4M2.SLDASM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]
2019-11-13 add moveo stl file for cura
2019-11-20 removeo Base assembly
    [1.SLDASM, 1M1B.SLDPRT, 1M2A-1.SLDPRT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]
2019-11-28 fixed stepper driver footprint
    [uStepper.PcbDoc, uStepper.SchDoc]
2019-11-29 Fix Home A
    [Configuration.h]
2019-11-29 fix Pully M8 IGNIS Belt groove
    [Pulley 8mm IGNIS.SLDPRT, Pulley 8mm IGNIS.STL]
2019-11-30 add gap at rotary plate
    [1M1B.SLDPRT, Pulley 8mm IGNIS.SLDPRT, Pulley 8mm IGNIS.STL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]
2019-12-02 Fix G29
    [Configuration.h]
2019-12-06 Fix a、b、c
    [Configuration.h]
2019-12-10 change a_m1、b_m1、c_m1
2019-12-10 Solve encoding garbled
    [Configuration_adv.h]
2019-12-10 split 4M1D
    [2M1 assembly.SLDASM, 3M1.SLDASM, 3M2.SLDASM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]
2019-12-12 Change the zeroing order and LCD No question mark displayed
    [Configuration.h]
2019-12-12 Fix G29 and speed
    [Configuration.h]
2019-12-13 Fix speed and add z probe spacing
    [Configuration.h]
2019-12-17 Fix G29 Step down
    [Configuration.h]
2019-12-17 Fix G29 and Add Lcd display
    [Configuration.h]
2019-12-17 change 2M2MA
    [2M1 assembly.SLDASM, 2M2.SLDASM, 2M2MA.SLDPRT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]
2019-12-18 update 4M1D in BNC3D-Moveo
    [3M1.SLDASM, 3M2.SLDASM, 3M2CC.SLDPRT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]
2019-12-27 add L636 connector
    [1M2A.SLDPRT, L636-female.SLDPRT, L636-male.SLDPRT]
2019-12-30 add conector housing in 1M2A
    [1M2A-2.SLDPRT, 1M2A.SLDPRT, Rotary Plate.SLDASM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]
2020-01-02 Change PROBE_OFFSET
    [Configuration.h]
2020-01-04 G30 Glass measuring platform
    [Configuration.h]
2020-01-06 Fix Planner finish Disable stepper and M18 Disable stepper
2020-01-06 Fix G30 and G28
    [Configuration.h]
2020-01-08 export STL file
    [1M2A-1.STL, 1M2A-2.STL, 1M2A.SLDPRT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]
2020-01-08 Change G29 Probe Mode
2020-01-15 chagne printer stl
2020-01-15 change Moveo.stl and Moveo.SLDPRT
2020-02-05 add AC power connector to Contorl Box
    [Control Box A.SLDPRT, Control Box.SLDASM, IEC-C13.SLDPRT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]
2020-02-07 remove gap between 5M1 and extruder stepper
    [4M_installHelper.SLDPRT, 4M_installHelper.STL, 5M1.SLDPRT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]
2020-02-08 add 3M_installHelper
    [3M_installHelper.SLDPRT]
2020-02-10 split Control box
    [4M_installHelper.SLDPRT, Control Box A-1.SLDPRT, Control Box A.SLDPRT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]
2020-02-10 add 2M_installHelper
    [2M_installHelper.SLDPRT]
2020-02-19 add 5x15x20_washer
    [4M2.SLDASM, 5x15x20_washer.SLDPRT, E3D All Metal Hotend V6 assy.SLDASM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]
2020-03-14 add wire label
    [4M2.SLDASM, M1 Tensor D.SLDASM, Tapa 4M1C_end switch.SLDASM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]
2020-03-21 add DuPont_cableDrop
    [DuPont_cableDrop.SLDPRT]
2020-04-06 5x15x10 washer
    [5x15x10_washer.SLDPRT, E3D All Metal Hotend V6 assy.SLDASM, Fan-DC-KDE0503PFB3-Promoco.sldasm]
2020-04-06 update BNC3D Moveo assembly
    [1M1A.SLDPRT, Rotary Plate.SLDASM, Sistema rodaments.SLDASM]

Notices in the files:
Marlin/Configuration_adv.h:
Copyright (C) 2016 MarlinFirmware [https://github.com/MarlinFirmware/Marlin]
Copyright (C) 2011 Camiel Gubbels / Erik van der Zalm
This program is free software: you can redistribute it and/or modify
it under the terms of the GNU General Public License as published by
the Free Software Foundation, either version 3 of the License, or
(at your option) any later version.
